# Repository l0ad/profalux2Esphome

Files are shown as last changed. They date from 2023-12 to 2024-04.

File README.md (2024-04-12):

# Profalux 868MHz (not _ZigBee_) roller shutter integration to EspHome/HA

> This project has been made with the help of [Tam](https://github.com/TamGit) and [Gérard/F6EEQ](https://github.com/F6EEQ).

<a href= "img/EMPX-B1.jpg">
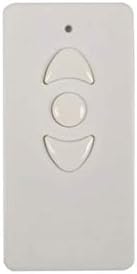
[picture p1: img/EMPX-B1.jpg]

</a>
&nbsp;
<br/><br/><br/><br/>

Prior to Zigbee adoption, Profalux roller shutter / remote communications were relying on a 868MHz protocol using [rolling codes](https://en.wikipedia.org/wiki/Rolling_code).

The most common remote, usually shipped with roller shutter, is a 3 buttons `MAI-EMPX-B1` model.

Such shutters can be controlled by several remotes, each remote can be paired to several shutters. See this document (in french) for [pairing a new remote](https://static.1001telecommandes.com/documents/1001-notice-profalux-empxb1.pdf) to an already paired couple of roller shutter / remote.

<br/><br/>

With the help of a [*Flipper Zero*](https://docs.flipper.net), each of the 3 commands sent by the remote to the shutter when pressing `up` / `down` / `stop` can be easily captured but replaying these commands is also not an option since commands contain rolling codes protecting shutters from replay attacks.

**So, the best option remains to emulate button press with a micro-controller connected to the remote.**

To get *Home Assitant* being able to control roller shutters, remote integration to *EspHome / HA* is performed through 2 main steps:

- **connect the remote to an ESP8266** micro-controller to emulate button press actions
- **setting up an EspHome device** exposing buttons, and integrate it to HA if needed.
<br/><br/>

> N.B. the idea is also to keep remote **as usable as before as possible**, meaning that **buttons could still be pressed by someone real** ;-)

The following gives details about the journey.

## Table of contents 
<!-- TOC start (generated with https://github.com/derlin/bitdowntoc) -->

- [A few words about the remote](#a-few-words-about-the-remote)
- [Step 1: Figuring things out ](#step-1-figuring-things-out)
- [Step 2: Pressing remote buttons using a micro-controller.](#step-2-pressing-remote-buttons-using-a-micro-controller)
	* [Soldering a connector with `GND` pin](#soldering-a-connector-with-gnd-pin)
   * [Connecting the ESP](#connecting-the-esp)
   * [PoC Arduino sketch](#poc-arduino-sketch)
- [Step 3: Making it the EspHome/HA way](#step-3-making-it-the-esphomeha-way)
   * [Configuration 1: easy but with cons](#configuration-1-easy-but-with-cons)
   * [Configuration 2: Making button pressable again](#configuration-2-making-button-pressable-again)
- [A case, just in case ;-)](#a-case-just-in-case-)

<!-- TOC end -->

<!-- TOC -->
## A few words about the remote

<a href= "img/EMPX-B1-board.png">
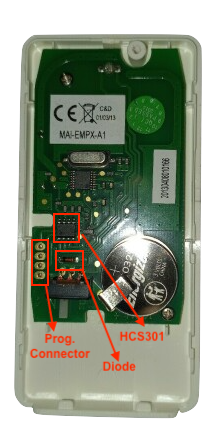
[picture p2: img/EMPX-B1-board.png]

</a>
</br></br></br></br>
&nbsp;

`MAI-EMPX-B1` remote is  built around a 868 MHz RF emitter and a [HCS301](https://ww1.microchip.com/downloads/en/devicedoc/21143b.pdf) rolling code / modulator chip. The HCS301 chip can handle up to 4 buttons, only 3 are used here.

&nbsp;
A **(unsoldered) 4 point connector** is accessible in order to program the HCS301 chip (store keys used for *KEELOQ*, ...)

&nbsp;
A **diode** protect the battery against receiving current from the outside through programming connector.

</br></br></br></br></br>

> By the way, **in order not to destroy any existing remote**, it s a good idea to search for a **spare one**. A brand new remote costs more or less 70 Euros but refurbished can be found for half that price.

<!-- TOC -->
## Step 1: Figuring things out 

<a href= "img/EMPX-B1-board-figuredOut.png">
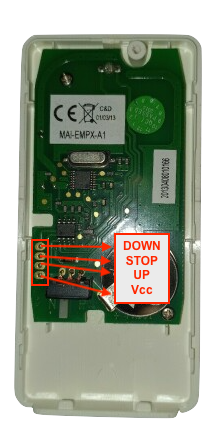
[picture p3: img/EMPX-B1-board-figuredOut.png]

</a>
&nbsp;
<br/><br/><br/><br/><br/><br/>
The wiring of the connector can easily be reversed by testing connections with HCS301 chip as well as with buttons pads on the back side. 
<br/><br/>
<a href= "img/EMPX-Back.jpg.jpg">
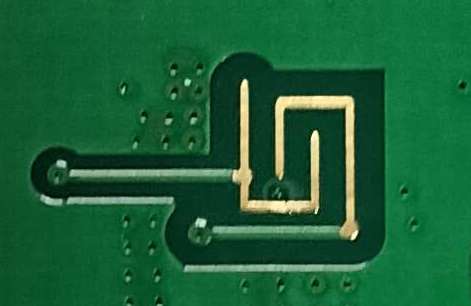
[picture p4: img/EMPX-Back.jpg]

</a>
<br/><br/>

**Pressing a button pulls input state to Vcc.**

<br/><br/><br/><br/><br/><br/><br/>

<a href= "img/EMPX-B1-board-figuredOut2.png">
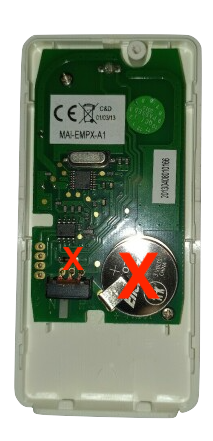
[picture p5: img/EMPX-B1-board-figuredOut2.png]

</a>
&nbsp;
<br/><br/><br/><br/><br/<br/><br/><br/>

As the remote will be connected to a USB-powered ESP board, the **battery is no longer needed**. 
<br/>

**Removing the battery however requires to shunt the protection diode. If not, RF emitter won't be supplied with power.**
<br/><br/><br/><br/><br/><br/><br/><br/>

<!-- TOC -->
## Step 2: pressing remote buttons using a micro-controller.

<!-- TOC -->
### Soldering a connector with `GND` pin

In order to connect the remote to the ESP, `GND` pin has to be provided.

This can be done simply by: 

- **drilling a fifth connector hole** besides `Vcc` 
- **soldering a 5 pin male header** on the connector pads
- **soldering** `Gnd` pin to a **ground location elsewhere**

<a href= "img/Profalux-Front-after.jpg">
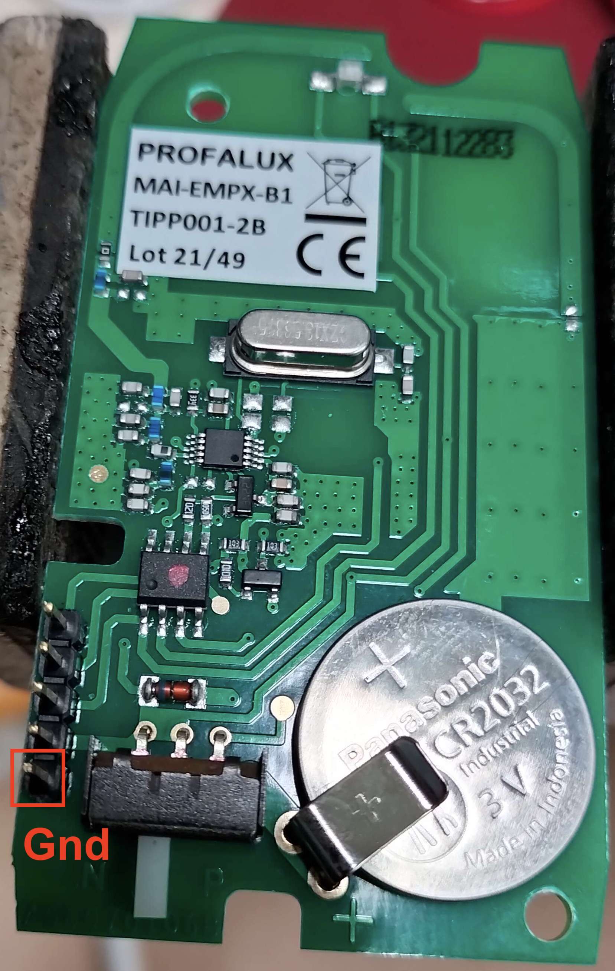
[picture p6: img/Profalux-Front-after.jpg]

</a>

<a href= "img/Profalux-Back-after.jpg">
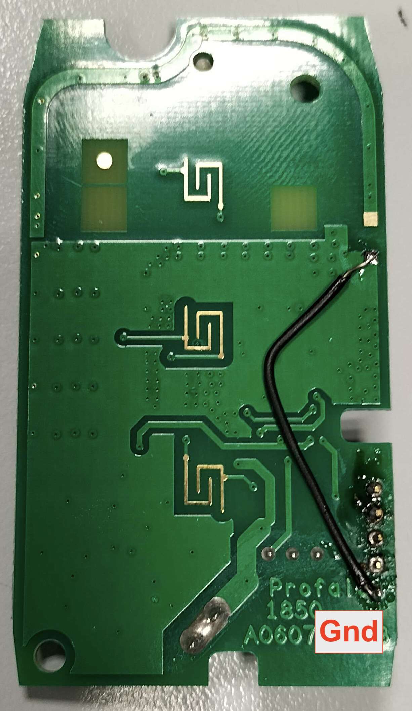
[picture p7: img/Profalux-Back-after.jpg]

</a>

<!-- TOC -->
### Connecting the ESP

<a href= "img/d1-mini-pinout.png">
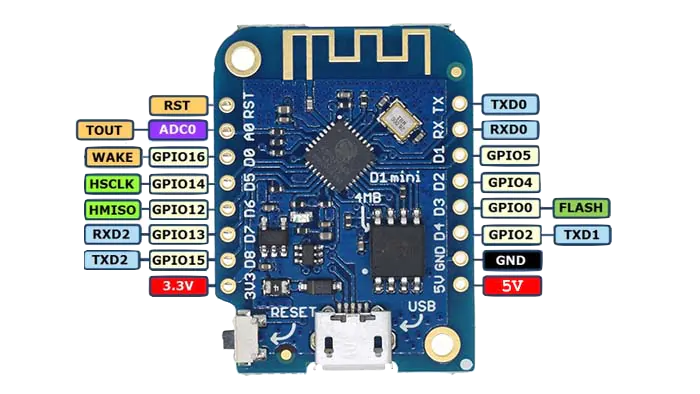
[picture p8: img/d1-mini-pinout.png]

</a>

The ESP used is an ESP8266-based [`Wemos D1 mini V3.0`](https://www.randomdiyprojects.it/wemos-d1-mini-v3-0-0/)

**Wiring** is the following:

| D1 mini side | Remote side |
|:---:|:---:|
| `D6` | `Down` |
| `D7` | `Stop` |
| `D8` | `Up` |
| `3.3V` | `Vcc` |
| `GND ` | `GND` |

<!-- TOC -->
### PoC Arduino sketch

The following [Arduino sketch](./Profalux2Esphome.ino) can be used to check if button press are properly emulated by the ESP: 

- by pairing the remote with the shutter and see if it rolls,
- by capturing traffic with a Flipper Zero (`Sub-GhZ` ->  `read`  / with scanning frequency set on `868MHz`).

> To get the D1 board working with Arduino IDE, refer to the [official documentation](https://www.wemos.cc/en/latest/tutorials/d1/get_started_with_arduino_d1.html).

```c
#define DOWN D6
#define STOP D7
#define UP D8

#define PULSE_DELAY 500
#define WAIT_DELAY 10000

void setup() {
  pinMode(UP, OUTPUT);
  pinMode(STOP, OUTPUT);
  pinMode(DOWN, OUTPUT);
  Serial.begin(9600);
}

void pressButtonAndWait(int pin) {
  Serial.println("DOWN");
  delay(10000);
  digitalWrite(DOWN, HIGH);
  delay(500);
  digitalWrite(DOWN, LOW);
}

void loop() {
  Serial.println("DOWN");
  pressButtonAndWait(DOWN);
  Serial.println("STOP");
  pressButtonAndWait(STOP);
  Serial.println("UP");
  pressButtonAndWait(UP);
}
```

<!-- TOC -->
## Step 3: Making it the EspHome/HA way

> To get the D1 board running EspHome firmware, refer to `Getting started` section of the [official documentation](https://esphome.io).

<!-- TOC -->
### Configuration 1: easy but with cons

Configuring the EspHome device is pretty straightforward, as buttons can be considered as [momentary swicthes](https://esphome.io/components/switch/gpio.html).

The **cons are nevertheless that physically pressing buttons will no longer work** because since GPIO pins are configured as `OUTPUT`, `LOW` (switch `OFF` state) state pulls pin to `GND` while pressing button pulls pin to `Vcc`.

The resulting [configuration file](./Profalux2Esphome-withoutButtons.yaml) (only relevant sections are shown) is below:

```yaml
esphome:
  name: profalux2esphome

esp8266:
  board: d1_mini_lite

# (missing elements like wifi, ... should be inserted here)
# ...
#

switch:
  - platform: gpio	
    pin: D6
    id: down
    name: "Down"
    on_turn_on:
    - delay: 500ms
    - switch.turn_off: down
    restore_mode: ALWAYS_OFF 
  - platform: gpio
    pin: D7
    id: stop
    name: "Stop"
    on_turn_on:
    - delay: 500ms
    - switch.turn_off: stop
    restore_mode: ALWAYS_OFF 
  - platform: gpio
    pin: D8
    id: up
    name: "Up"
    on_turn_on:
    - delay: 500ms
    - switch.turn_off: up
    restore_mode: ALWAYS_OFF 

web_server:
  port: 80

```

> `web_server` section is useful only when using EspHome without HA, to be able to toogle buttons through device dashboard.

<!-- TOC -->
### Configuration 2: Making button pressable again

In order to bring back physical buttons to life, GPIO pin mode has to be changed to `INPUT` when switch is in `OFF` state.

The resulting [configuration file](./Profalux2Esphome-withButtons.yaml) (only relevant sections are shown) is below:

```yaml
esphome:
  name: profalux2esphome

esp8266:
  board: d1_mini_lite

# (missing elements like wifi, ... here)
...
#

substitutions:
  down_pin: 'D6'
  stop_pin: 'D7'
  up_pin: 'D8'

output:
  - platform: gpio
    pin: ${down_pin}
    id: gpio_down
  - platform: gpio
    pin: ${stop_pin}
    id: gpio_stop
  - platform: gpio
    pin: ${up_pin}
    id: gpio_up

switch:
  - platform: output
    output: gpio_down
    id: down
    name: "Down"
    on_turn_on:     
    - lambda: |-
        pinMode(${down_pin}, OUTPUT);
        digitalWrite(${down_pin}, HIGH);     
    - delay: 500ms
    - switch.turn_off: down
    on_turn_off:     
    - lambda: |-
        pinMode(${down_pin}, INPUT);       
    restore_mode: ALWAYS_OFF 

  - platform: output
    output: gpio_stop
    id: stop
    name: "Stop"
    on_turn_on:     
    - lambda: |-
        pinMode(${stop_pin}, OUTPUT);
        digitalWrite(${stop_pin}, HIGH);     
    - delay: 500ms
    - switch.turn_off: stop
    on_turn_off:     
    - lambda: |-
        pinMode(${stop_pin}, INPUT);       
    restore_mode: ALWAYS_OFF 
  
  - platform: output
    output: gpio_up
    id: up
    name: "Up"
    on_turn_on:     
    - lambda: |-
        pinMode(${up_pin}, OUTPUT);
        digitalWrite(${up_pin}, HIGH);     
    - delay: 500ms
    - switch.turn_off: up
    on_turn_off:     
    - lambda: |-
        pinMode(${up_pin}, INPUT);       
    restore_mode: ALWAYS_OFF 
  
```

<!-- TOC -->
## A case, just in case ;-)

<a href= "img/EMPX-B1.jpg">
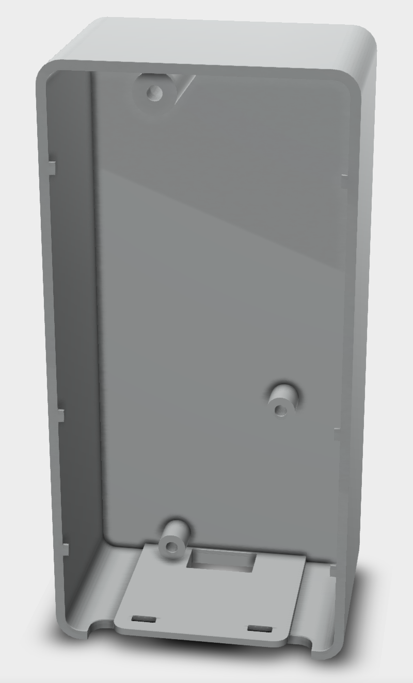
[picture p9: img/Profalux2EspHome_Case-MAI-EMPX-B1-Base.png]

</a>
&nbsp;
<br/><br/><br/><br/>

The original case was too thin to fit the ESP and connectors.

So, thanks to Tam who helped me to understand [FreeCad](https://www.freecad.org) basics and gave me hints to deal with it, i've made a **replacement case**.

**Model files**, in STL and STEP format, are availbale under `3D` subfolder. Enjoy it!

&nbsp;
<br/><br/><br/><br/>
<br/><br/><br/><br/>

Job done! <br/> [S.](https://github.com/sebastienjean)

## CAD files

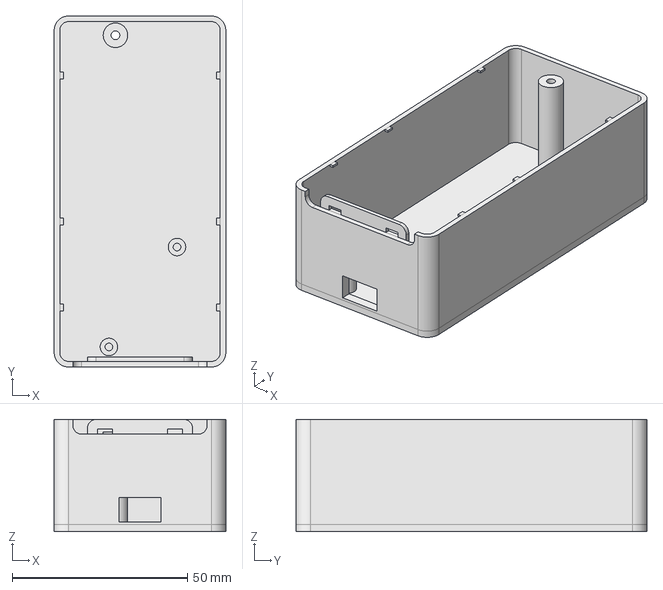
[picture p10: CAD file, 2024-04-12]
3D/Profalux2EspHome_Case-MAI-EMPX-B1-Base.step
49.0 x 100.2 x 32.0 mm

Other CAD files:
3D/Profalux2EspHome_Case-MAI-EMPX-B1-Base.stl

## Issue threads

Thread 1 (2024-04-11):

Fonctionnement sur batterie

titoftit, 2024-04-11:
Bonjour,

Merci pour ce tuto qui pourrait m'être très utile.
Je me demandais s'il serait possible de faire marcher la télécommande sur batterie ou avec des piles, plutôt que de devoir la brancher sur un usb ?

Autre question, vous utilisez un arduino ESP8266 qui communique donc en Wifi, pourrait on imaginer un système en zigbee ? Je n'ai aucune idée si un module de ce genre existe, mais le zigbee est plus pratique dans mon cas car il permet de couvrir de plus longues distances.

Merci.

sebastienjean, 2024-04-12:
Bonjour,

Le choix de l'alimentation pour USB s'est imposé de par l'utilisation d'esphome, donc du wifi, qui nécessite de maintenir la connextion (et qui donc entraine une consommation d'énergie trop élévée au regard de l'autonomie de la batterie).

Effectivement, se tourner vers zigbee pourrait être la solution pour passer sur batterie. Je n'ai pour le moment par d'expérience sur le développement de devices HomeAssistant en Zigbee, mais j'essayerai de m'y pencher si j'en ai l'occasion.

Pour ce qui est de la portée, l'utilisation d'un esp avec antenne externe, ou d'un répéteur, pourrait néanmoins grandement améliorer les choses. De l'exéprience que j'ai avec Zigbee (avec un Lixee pbranché sur mon linky extérieur), la portée n'est pas meilleure, mais il est vrai que le réseau zigbee d'une installation domotique est souvent bien touffu.
